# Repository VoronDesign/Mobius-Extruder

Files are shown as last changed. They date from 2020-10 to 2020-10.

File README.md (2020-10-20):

# VORON M4 Extruder

Image of M4

This is the VORON M4 Extruder. It's a dual geared hobbed filament extruder designed for the Voron family of printers. It features a 4:1 belt driven design to provide torque while being able to be near silent. It borrows the best parts of the various extruders we've released over the past 5 years.

Voron Logo

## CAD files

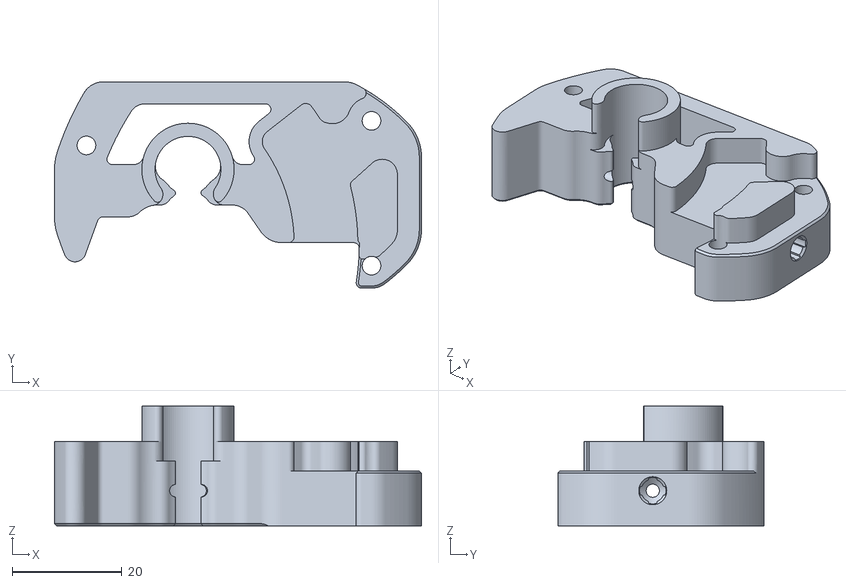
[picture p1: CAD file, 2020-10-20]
STLs/main_body_mirror.stl
66.8 x 37.6 x 21.8

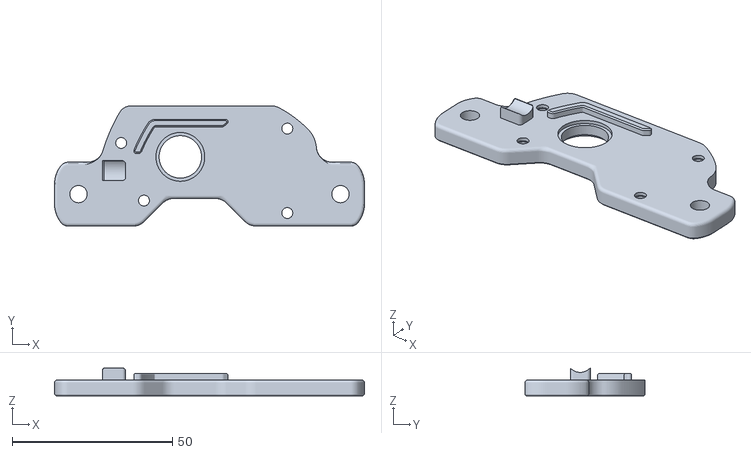
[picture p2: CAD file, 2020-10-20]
STLs/end_plate_mirror.stl
96.8 x 37.6 x 8.60

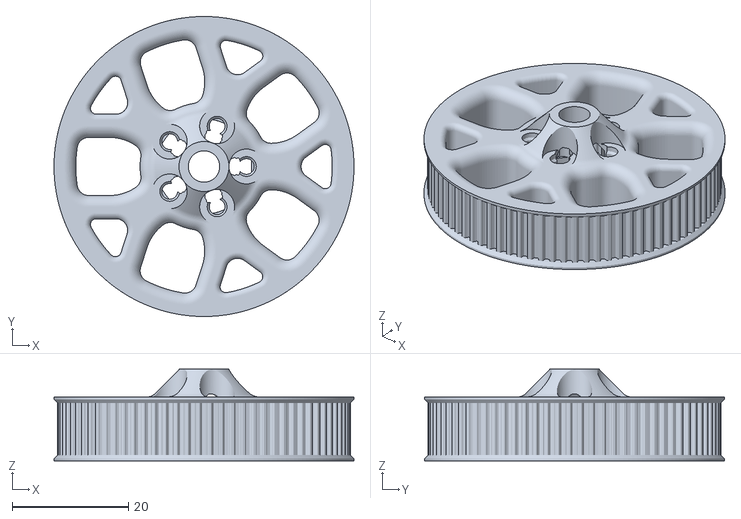
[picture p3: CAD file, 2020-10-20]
STLs/[a]_80t_gear.stl
51.6 x 51.6 x 15.8

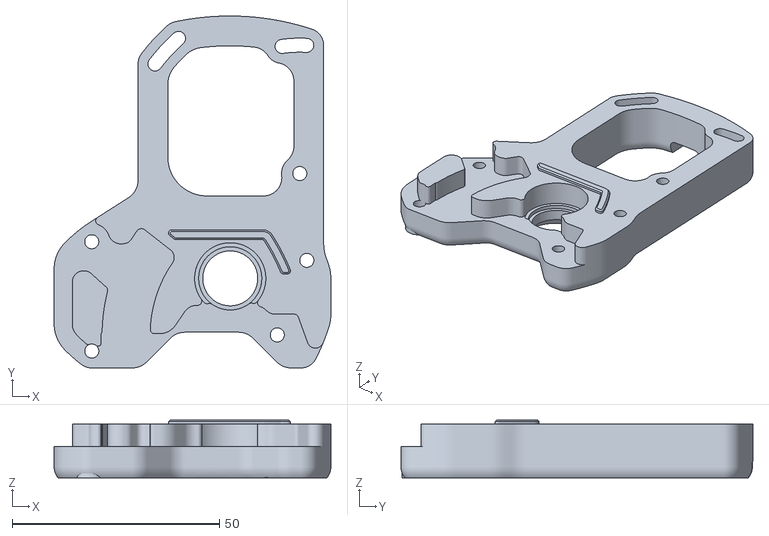
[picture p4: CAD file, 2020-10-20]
STLs/motor_plate_mirror.stl
66.8 x 85.0 x 14.0

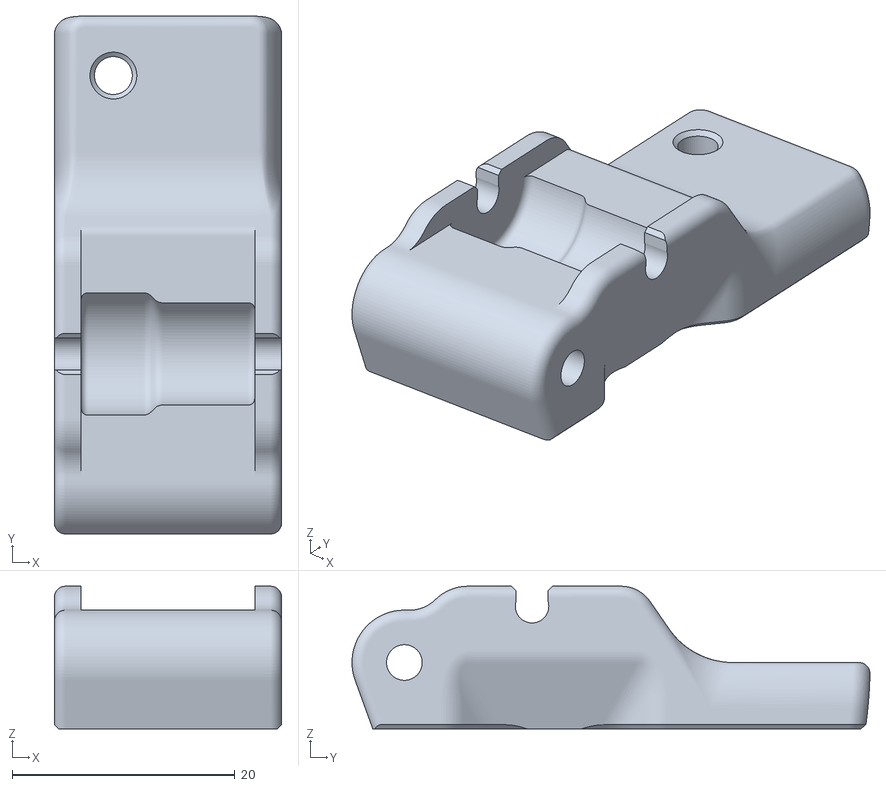
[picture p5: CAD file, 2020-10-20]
STLs/[a]_guidler.stl
20.4 x 46.5 x 12.8

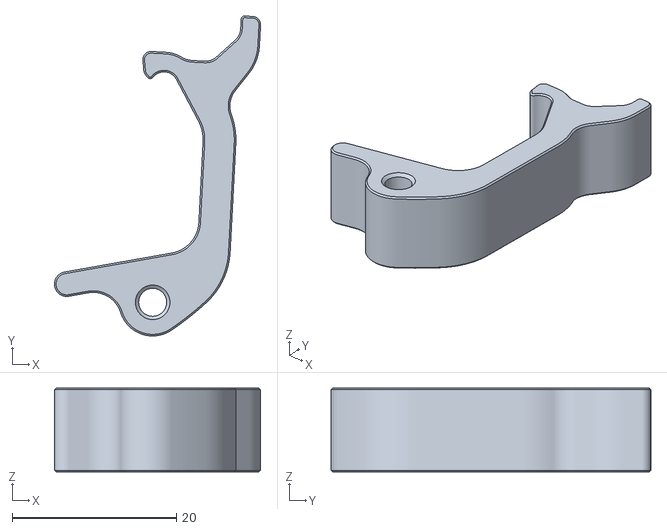
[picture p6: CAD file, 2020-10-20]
STLs/[a]_latch.stl
25.1 x 38.9 x 10.2

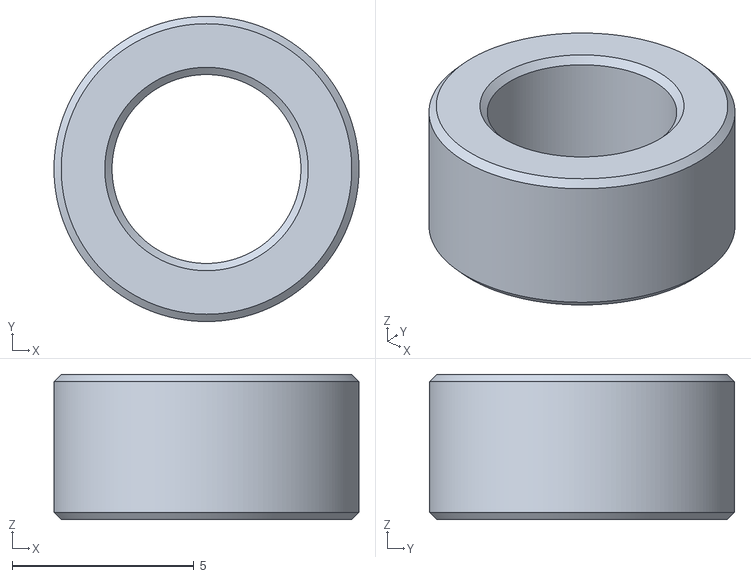
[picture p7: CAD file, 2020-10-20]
STLs/[a]_5x4mm_spacer.stl
8.40 x 8.40 x 4.00

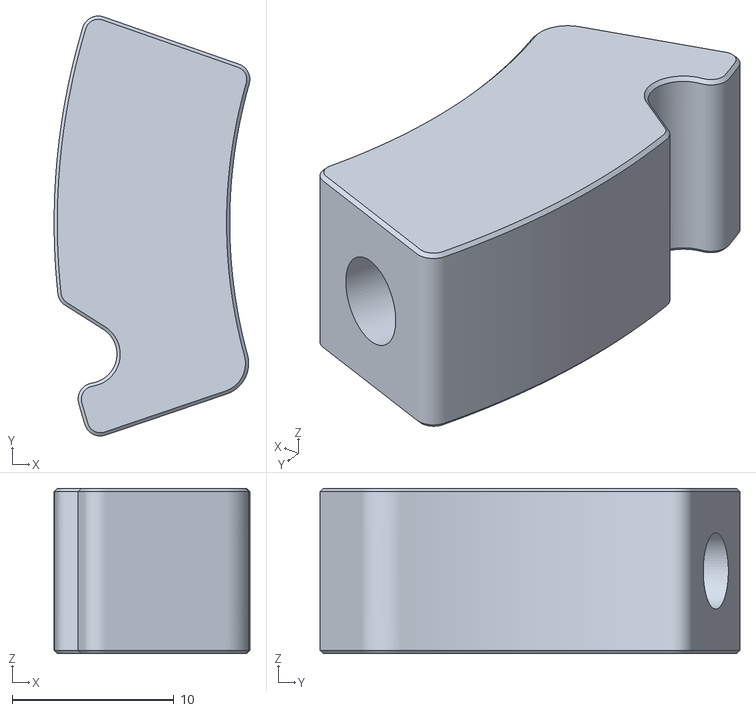
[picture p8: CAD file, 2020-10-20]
STLs/latch_shuttle.stl
12.1 x 25.9 x 10.2

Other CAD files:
STLs/main_body.stl
STLs/end_plate.stl
STLs/[a]_guidler_mirror.stl
STLs/motor_plate.stl
CAD/voron_m4_assembly.f3d

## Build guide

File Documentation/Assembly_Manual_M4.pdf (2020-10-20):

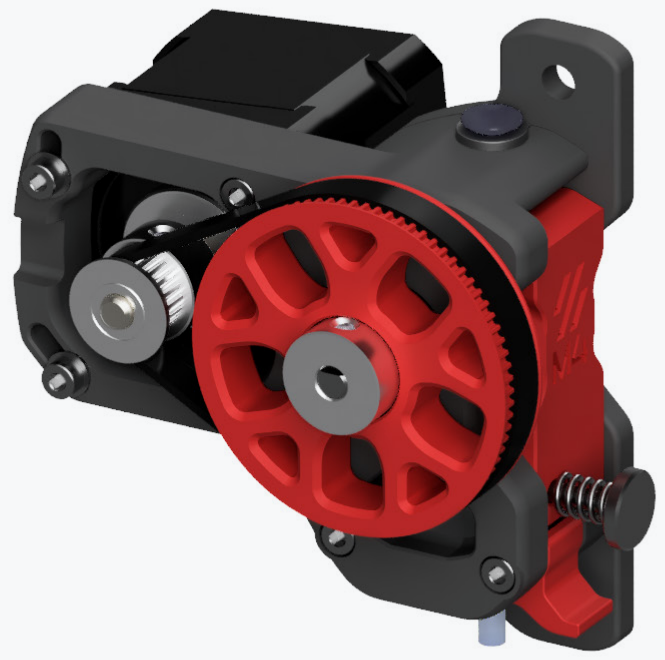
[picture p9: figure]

1

### WWW.VORONDESIGN.COM

VERSION 2020-10-19

# M4 ASSEMBLY MANUAL

## We build space shuttles with gardening tools

so anyone can have a space shuttle of their own.

# VORON

2

INTRODUCTION | WWW.VORONDESIGN.COM

Before you begin on your journey, a word of caution.

In the comfort of your own home you are about to assemble a robot. This
machine can maim, burn, and electrocute you if you are not careful. Please
do not become the first VORON fatality. There is no special Reddit flair for that.

Please, read the entire manual before you start assembly. As you begin wrenching, please check our Discord channels for any tips and questions that may halt your progress.

Most of all, good luck!
THE VORON TEAM

3

INTRODUCTION | WWW.VORONDESIGN.COM

PART PRINTING GUIDELINES
The Voron Team has provided the following print guidelines for you to follow in order to have the best chance at success with your parts. There are often questions about substituting materials or changing printing standards, but we recommend you follow these.

3D PRINTING PROCESS
Fused Deposition Modeling (FDM)

MATERIAL
ABS

LAYER HEIGHT
Recommended: 0.2mm

EXTRUSION WIDTH
Recommended: Forced 0.4mm

INFILL TYPE
Grid, Gyroid, Honeycomb, Triangle or Cubic

INFILL PERCENTAGE
Recommended: 40%

WALL COUNT
Recommended: 4

SOLID TOP/BOTTOM LAYERS
Recommended: 5

PRINT IT FORWARD (PIF)
Often times our community members have issues printing ABS will bootstrap themselves into a VORON using our Print It Forward program. This is a service where approved members with VORON printers can make you a functional set of parts to get your own machine up and running.
Check Discord if you have any interest in having someone help you out.

4

INTRODUCTION | WWW.VORONDESIGN.COM

HOW TO GET HELP
If you need assistance with your build, we’re here to help. Head on over to our Discord group and post your questions. This is our primary medium to help VORON Users and we have a great community that can help you out if you get stuck.

https://discord.gg/voron

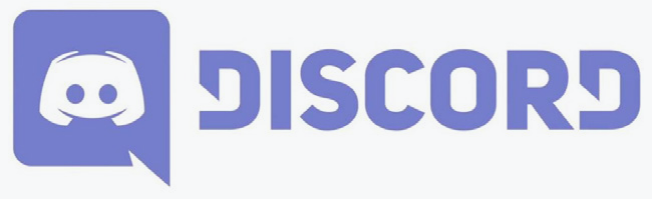
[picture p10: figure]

THIS IS JUST A REFERENCE
This manual is designed to be a simple reference manual. Building a Voron can be a complex endeavour and for that reason we recommend downloading the CAD files off our Github repository if there are sections you need clarification on. It can be sometimes be easier to follow along when you have the whole assembly in front of you.

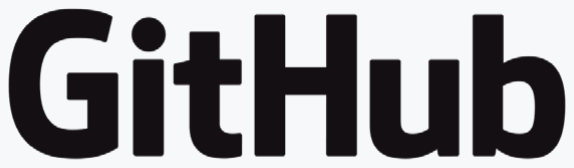
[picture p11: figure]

https://github.com/vorondesign

5

### WWW.VORONDESIGN.COM

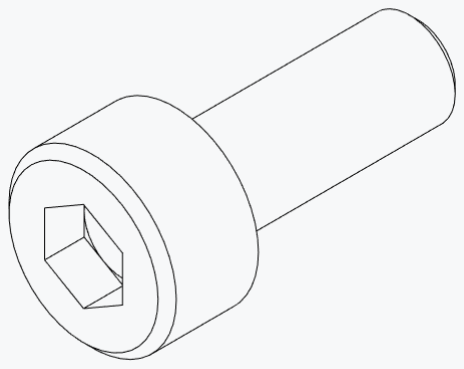
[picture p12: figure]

SOCKET HEAD CAP SCREW (SHCS) Metric fastener with a cylindrical head and hex drive. The most common fastener used on the Voron.

ISO 4762

WASHER
Small metal disc to increase the surface area.

DIN 988

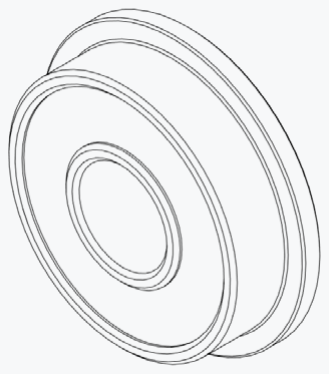
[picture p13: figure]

PULLEY
GT2 pulley used on the motion system of the Voron.

HARDWARE
HEAT SET INSERT
Heat inserts with a soldering tip so that they melt the plastic when installed. As the plastic cools, it solidifies around the knurls and ridges on the insert for excellent resistance to both torque and pull-out.

F695 BEARING
A ball bearing with a flange used in various gantry locations.

GRUB SCREW
Small headless screw with an internal drive.

ISO 4026

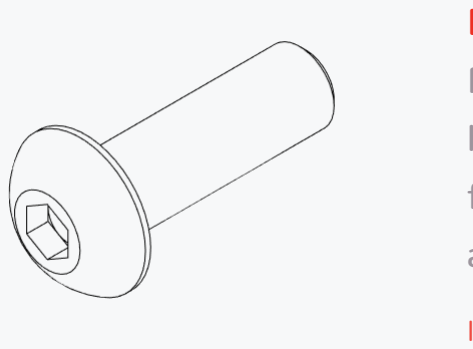
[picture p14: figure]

BUTTON HEAD CAP SCREW (BHCS) Metric fastener with a domed shape head and hex drive. Most commonly found in locations where M5 fasteners are used.

ISO 7380-1

### WWW.VORONDESIGN.COM

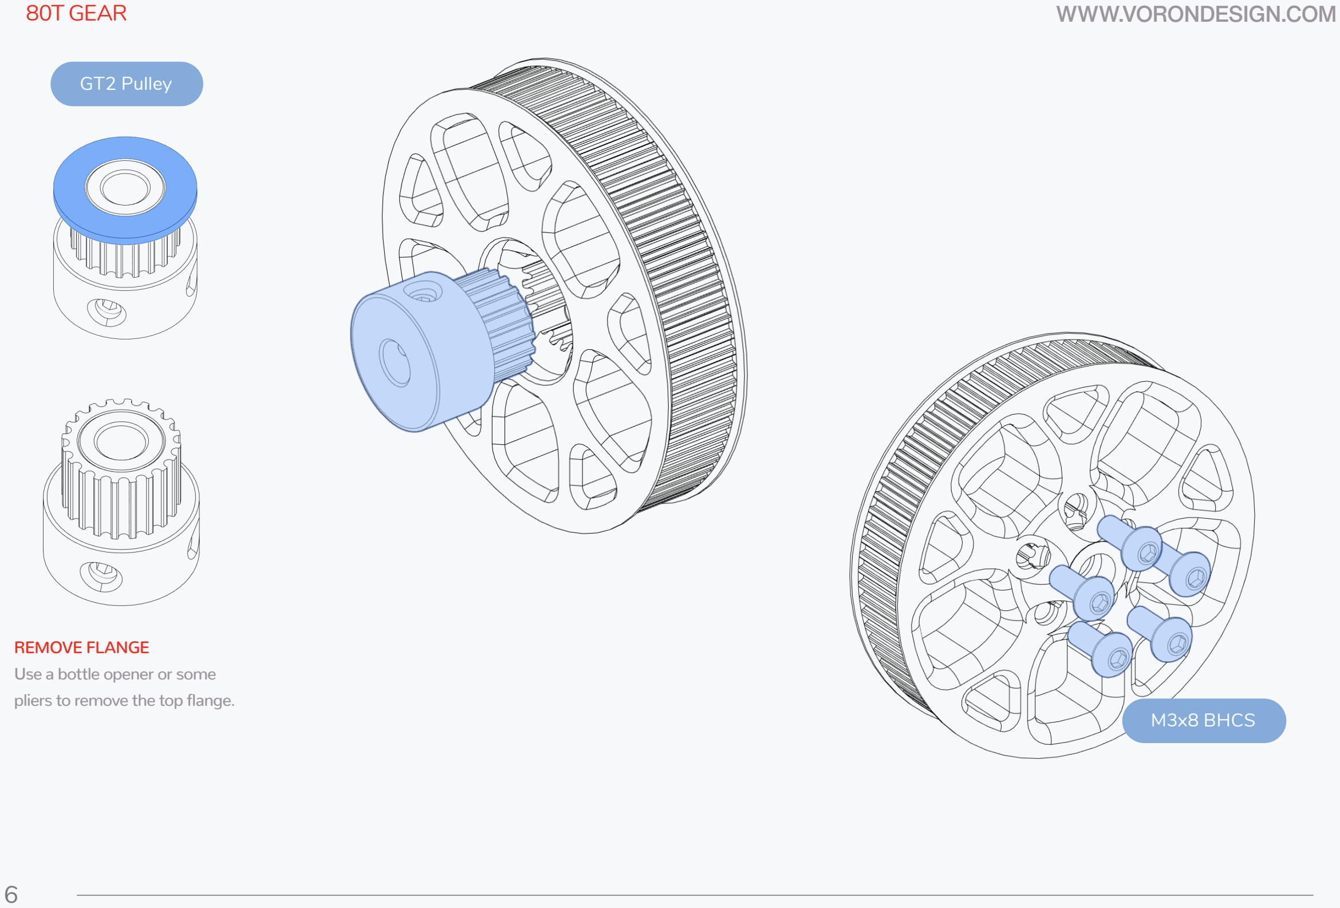
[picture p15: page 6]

6

REMOVE FLANGE
Use a bottle opener or some pliers to remove the top flange.

GT2 Pulley

M3x8 BHCS

80T GEAR

7

### WWW.VORONDESIGN.COM

CHECK BEARING FIT
The bearings must slip on and off the shaft easily. Pressing the bearings on the shaft will damage them. Lightly sand the shaft if required.

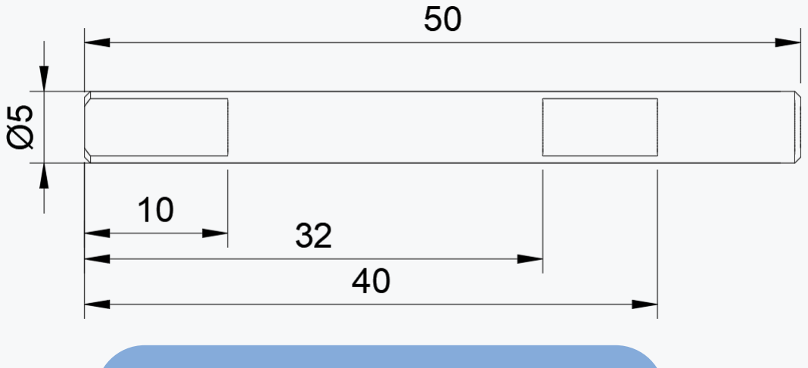
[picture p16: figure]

5x50mm Shaft w/ Flats
F695 Bearing

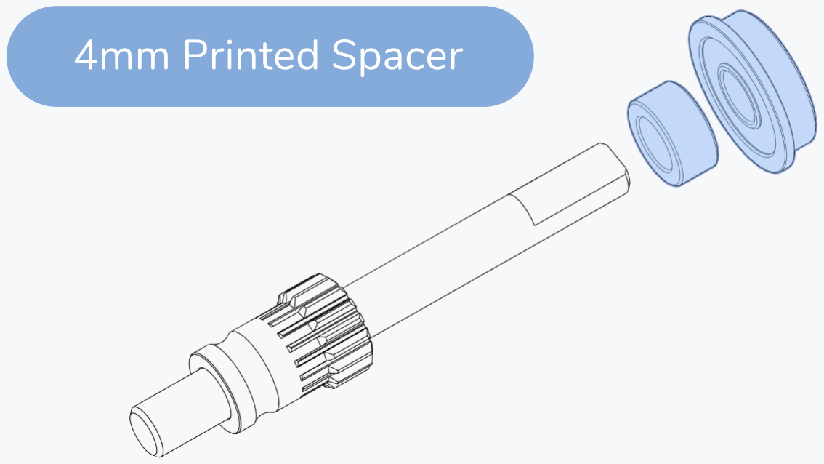
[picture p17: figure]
4mm Printed Spacer

DRIVE GEAR POSITION
Position the drive gear 8mm from the end of the shaft and tighten the grub screw.
Use thread locker.

DRIVE SHAFT

FLAT FACE ON THE SHAFT
Align the flat face of the shaft with the grub screw of the drive gear. If your shaft is fully round make a small flat spot with a file to ensure proper seating.

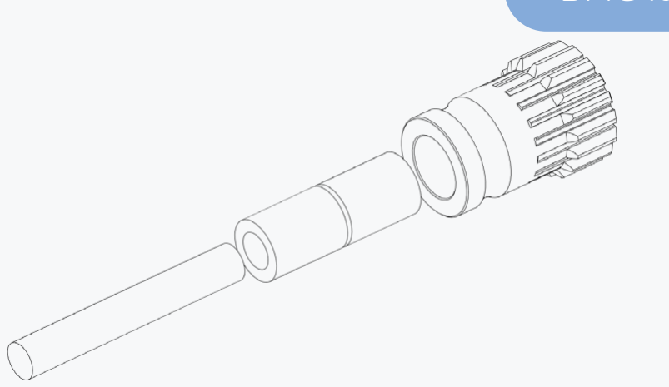
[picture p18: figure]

8

### WWW.VORONDESIGN.COM

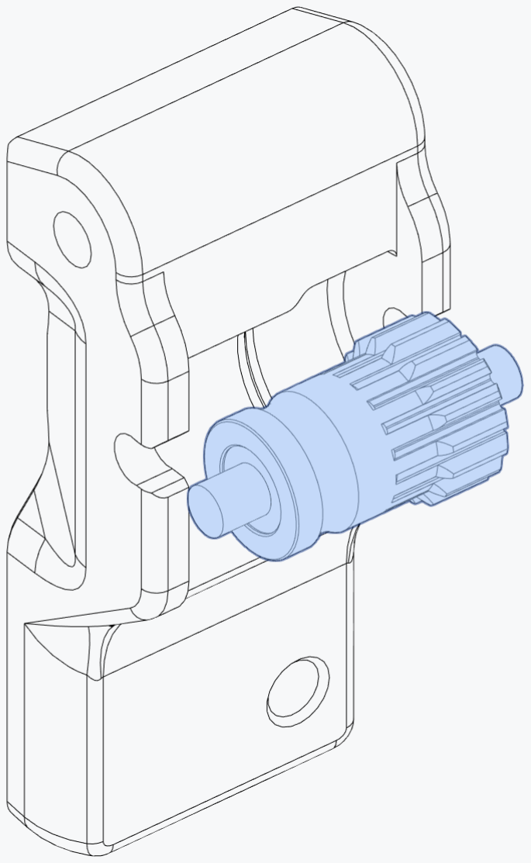
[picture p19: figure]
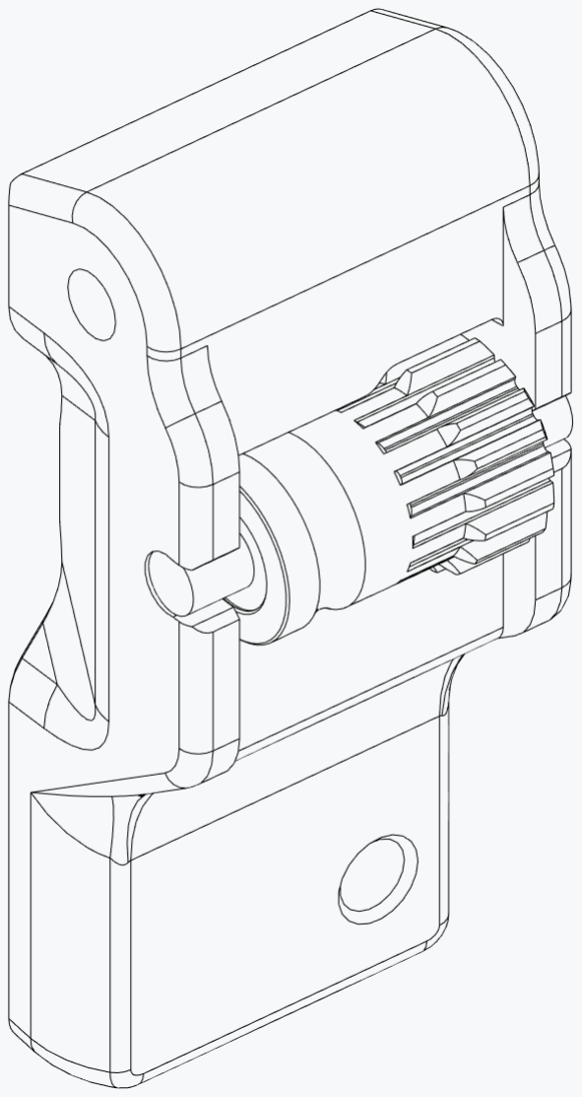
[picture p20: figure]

LUBRICATE BEARINGS
A light lubrication film will help with smooth operation and longevity.

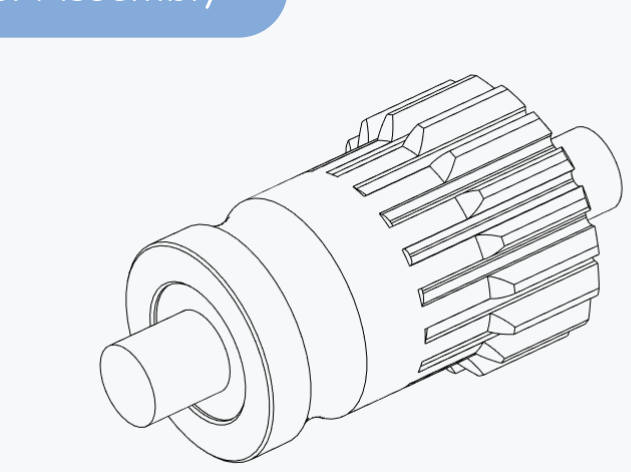
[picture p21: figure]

BMG Idler Assembly

IDLER ASSEMBLY

### WWW.VORONDESIGN.COM

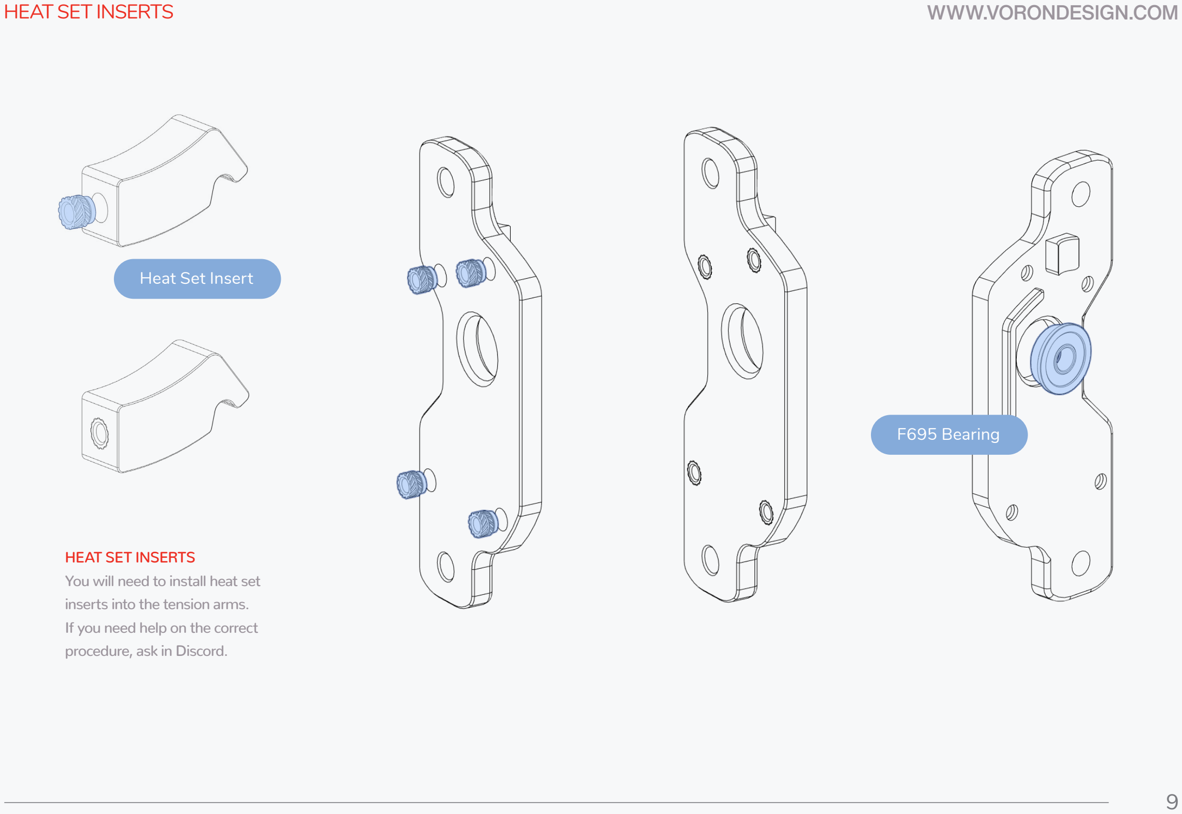
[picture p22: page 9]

9

HEAT SET INSERTS
You will need to install heat set inserts into the tension arms. If you need help on the correct procedure, ask in Discord.

Heat Set Insert

F695 Bearing

HEAT SET INSERTS

BODY ASSEMBLY | WWW.VORONDESIGN.COM

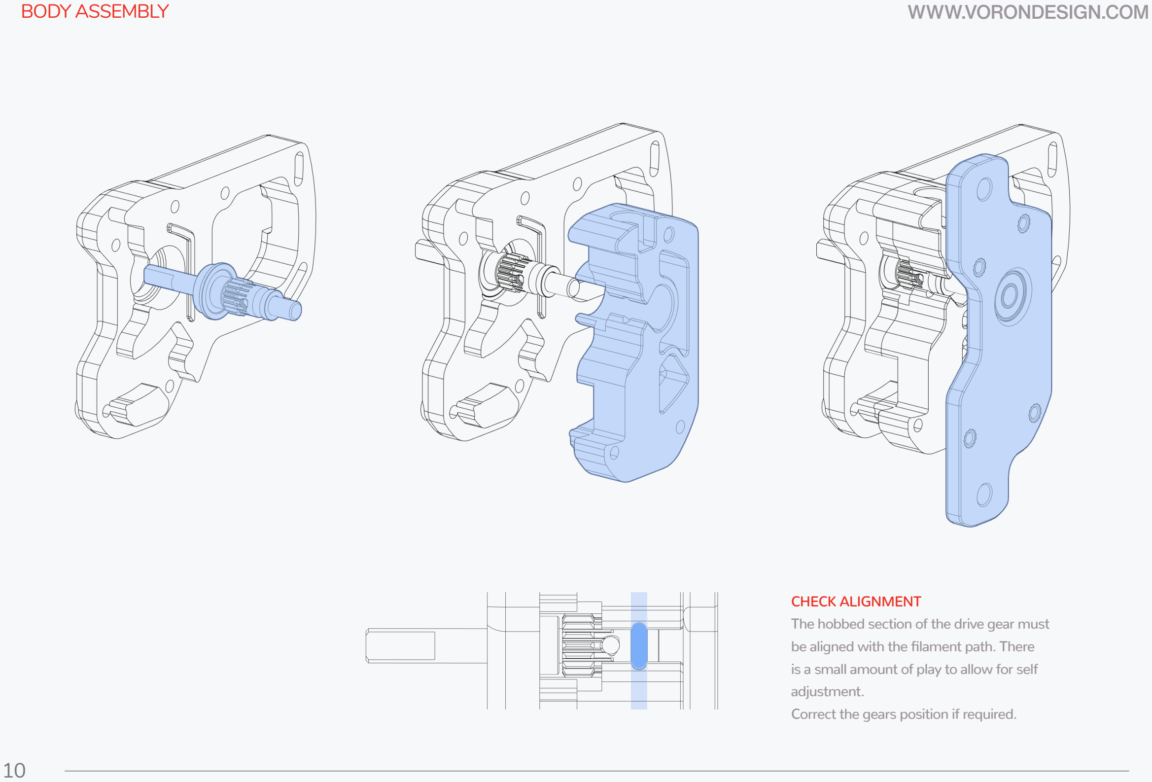
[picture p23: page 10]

10

CHECK ALIGNMENT
The hobbed section of the drive gear must be aligned with the filament path. There is a small amount of play to allow for self adjustment.
Correct the gears position if required.

BODY ASSEMBLY | WWW.VORONDESIGN.COM

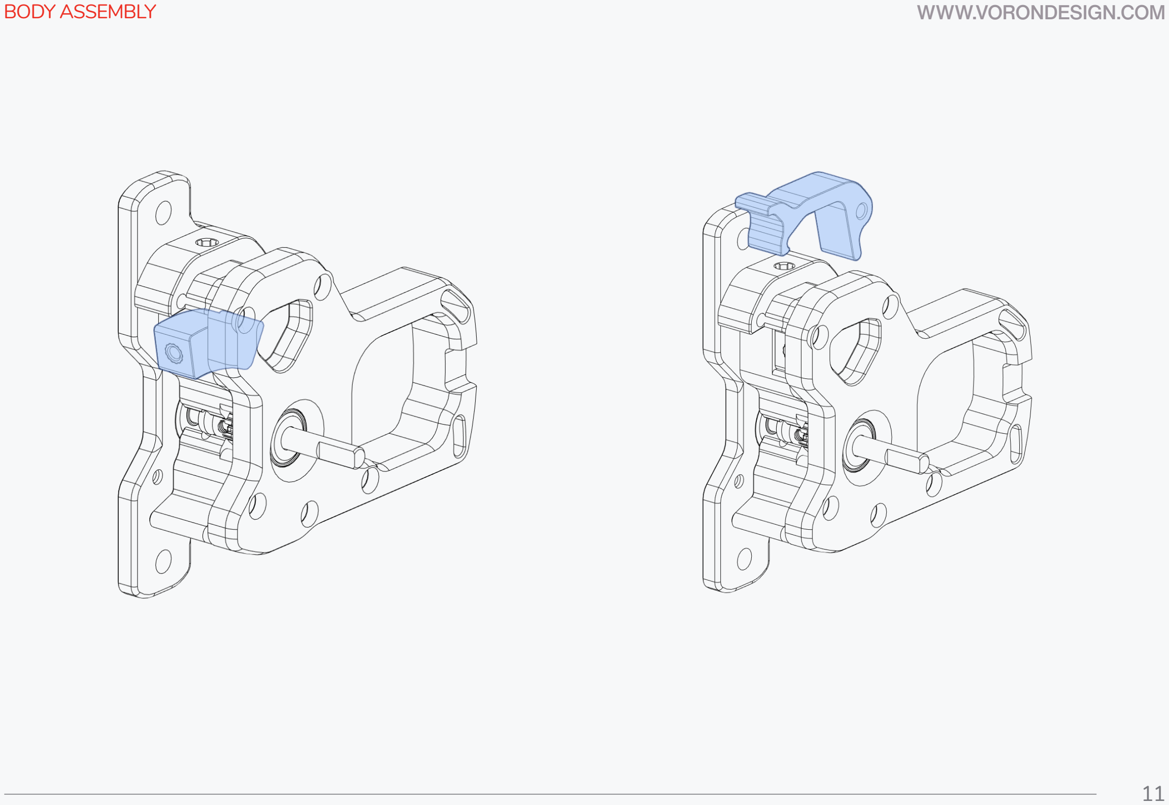
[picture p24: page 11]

11

12

### WWW.VORONDESIGN.COM

BODY ASSEMBLY

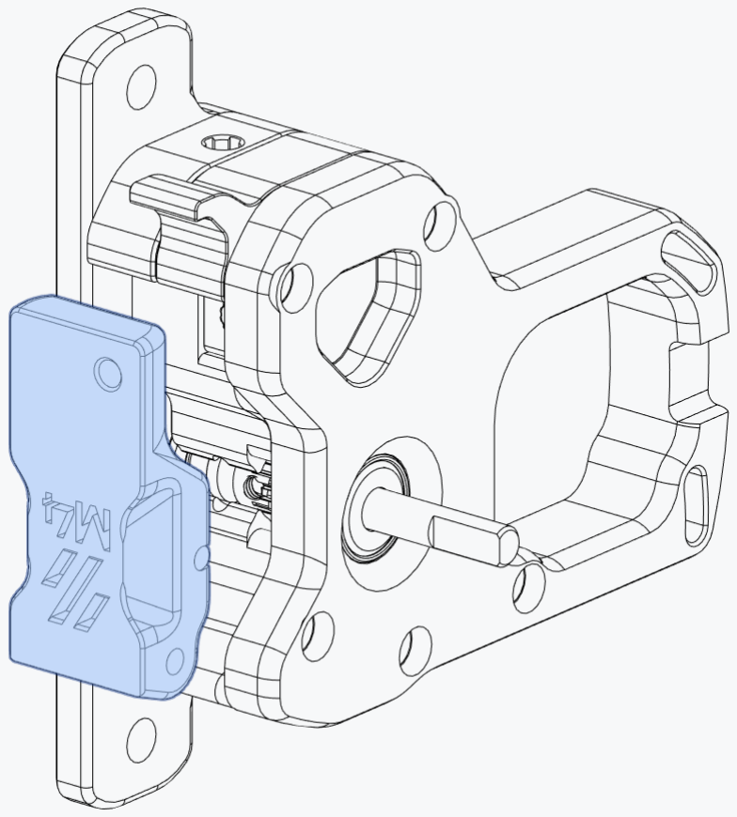
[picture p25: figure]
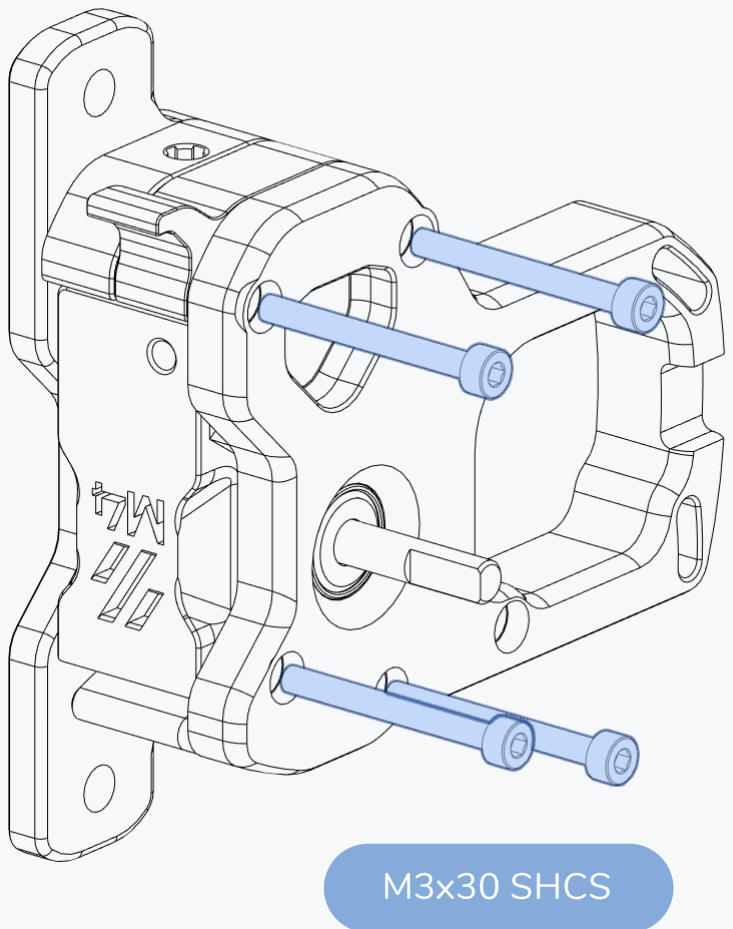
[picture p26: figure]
M3x30 SHCS

### WWW.VORONDESIGN.COM

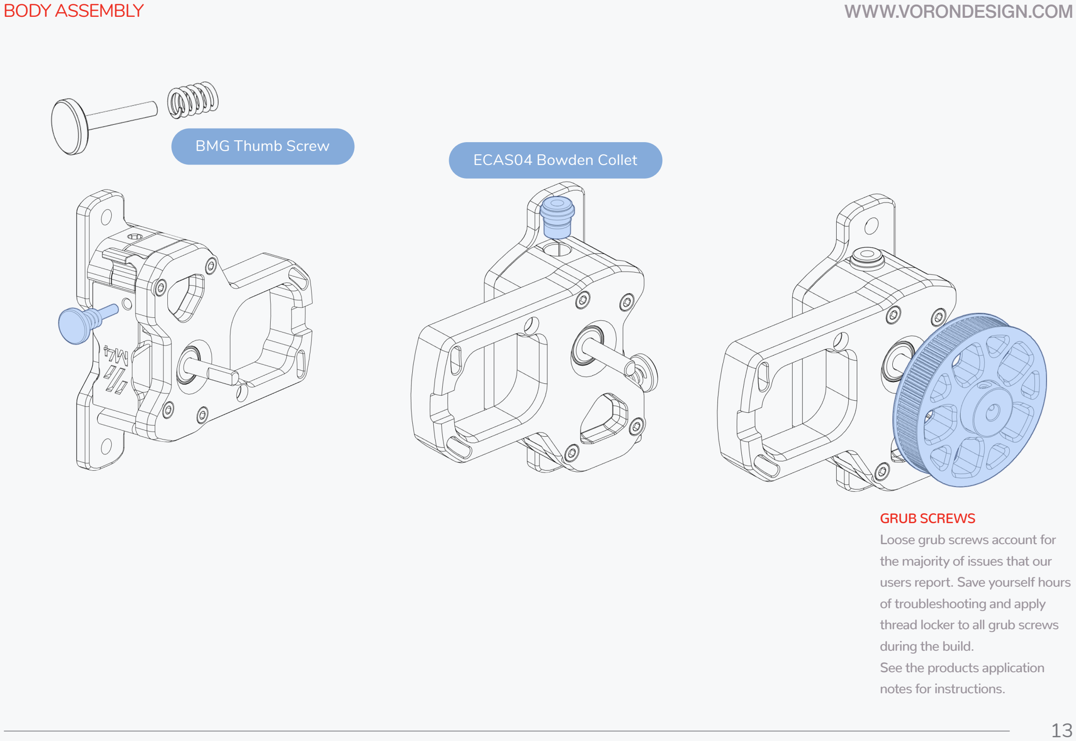
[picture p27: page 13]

13

GRUB SCREWS
Loose grub screws account for the majority of issues that our users report. Save yourself hours of troubleshooting and apply thread locker to all grub screws during the build.
See the products application notes for instructions.

BMG Thumb Screw
ECAS04 Bowden Collet

BODY ASSEMBLY

### WWW.VORONDESIGN.COM

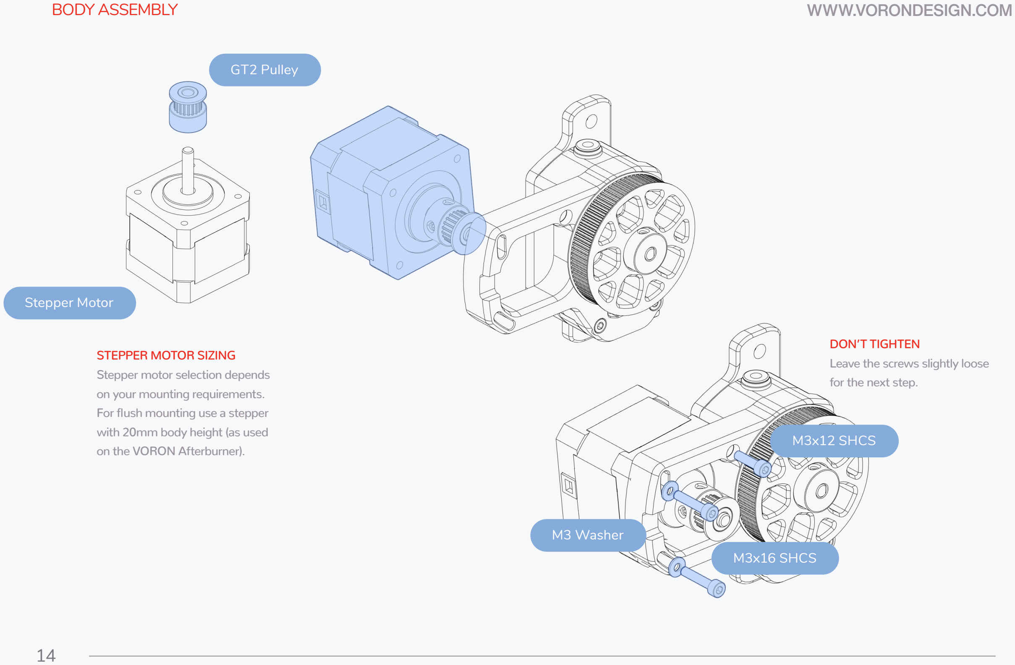
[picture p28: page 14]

14

GT2 Pulley

Stepper Motor

STEPPER MOTOR SIZING
Stepper motor selection depends on your mounting requirements. For flush mounting use a stepper with 20mm body height (as used on the VORON Afterburner).

M3x12 SHCS

M3x16 SHCS

M3 Washer

DON’T TIGHTEN
Leave the screws slightly loose for the next step.

BODY ASSEMBLY

15

### WWW.VORONDESIGN.COM

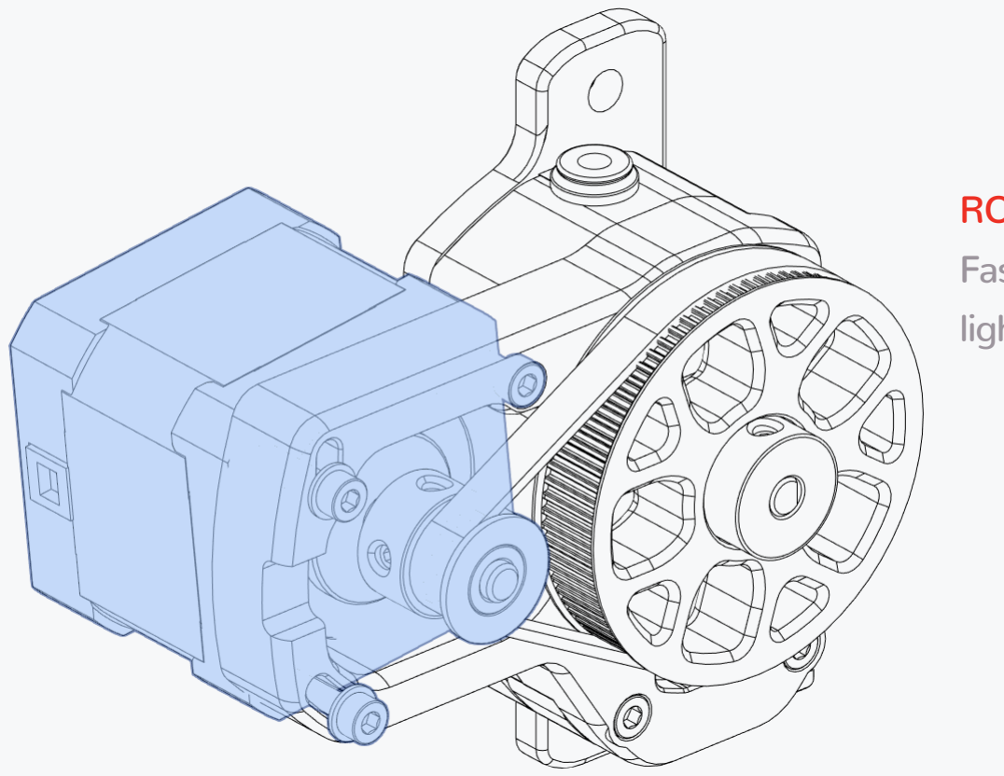
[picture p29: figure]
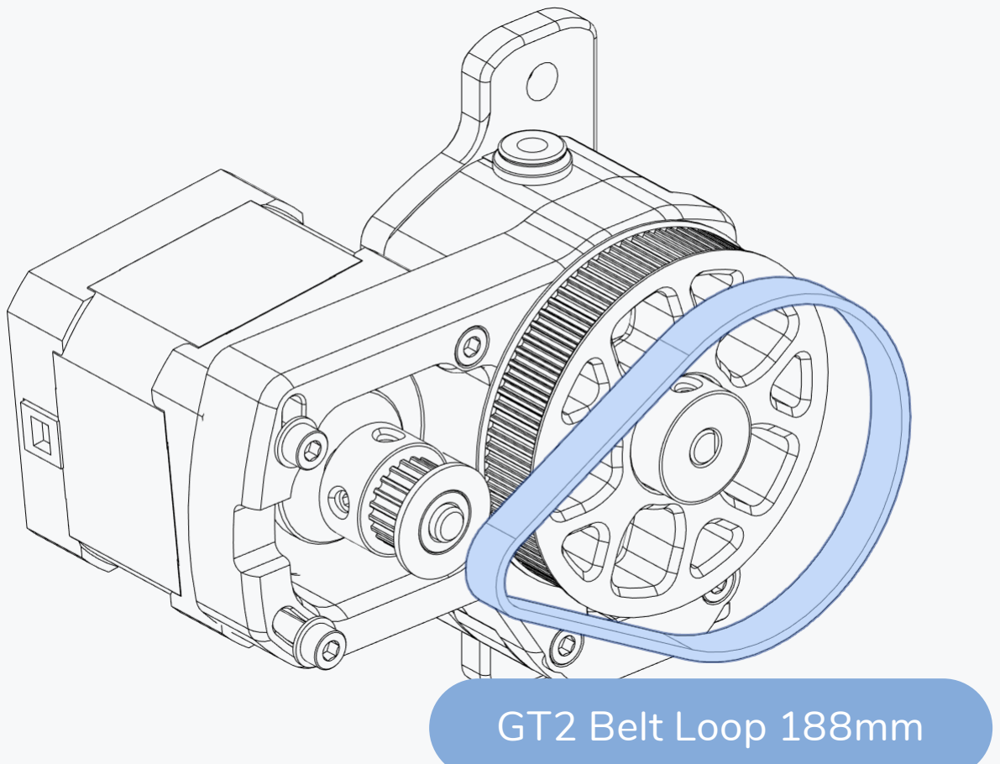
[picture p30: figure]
GT2 Belt Loop 188mm

ROTATE STEPPER TO TIGHTEN
Fasten the screws after applying a light pressure to tighten the belt.

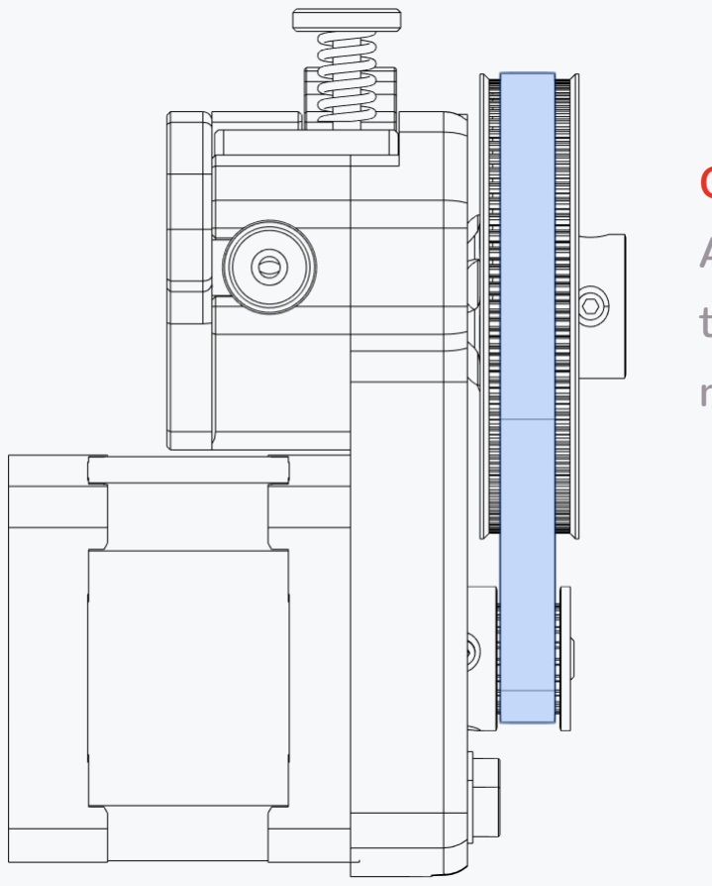
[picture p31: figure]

CHECK ALIGNMENT
Adjust the position of the pulley on the stepper if required. Belt must not rub on the flanges.

DRIVE BELT & ALIGNMENT

16

### WWW.VORONDESIGN.COM

Github
https://github.com/vorondesign

Website
www.vorondesign.com

Discord
https://discord.gg/voron

# VORON

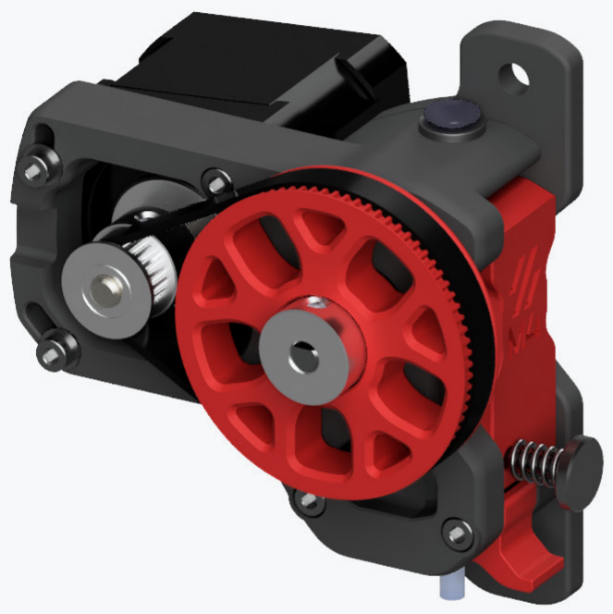
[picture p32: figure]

17

### WWW.VORONDESIGN.COM

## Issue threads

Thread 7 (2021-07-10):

80-Tooth to 20-Tooth gear connection screw: Size mismatch between sources

SobhanAbedi, 2021-07-10:
Hi. The main issue is with VoronDesing website. I think since the website is linked under VoronDesign GitHub account, it's ok to post this issue here.
The screw needed for connecting the 80-Tooth gear to 20-Tooth gear is said to be M3x6 in the BOM and Sourcing guide but in the manual and .STEP file it is M3x8. Since M3x8 doesn't have any clearance issues in the CAD, I guess they should both work fine but it would be better if the mismatch is fixed.

telxoid, 2021-08-20:
Confirmed and pointed out by another user.  Either should work fine, but best to eliminate confusion.

Closed 2022-07-19.

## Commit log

2018-09-08 Mobius 2 Extruder
    [80t_press_bolt_head_side.STL, 80t_press_hex_side.STL, _belt_clip_x2.stl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]
2018-10-17 replacing 80T STL's
    [80t_ring_gear.stl, _vlock_a.stl, _vlock_b.stl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]
2018-10-17 sorry about earlier. I didn't mean to touch you in that way. :(
    [_vlock_a.stl, _vlock_b.stl, _vlock_ring_80t.stl]
2019-01-27 Branch reorg for Mobius
    [01_home_z_mech.g, 01_physics_z_100.g, 01_physics_z_1000.g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]
2019-02-20 Removing a space cause it bothers me
    [_external_gear_spacer.stl, _front_idler_arm.stl, _internal_gear_spacer.stl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]
2019-02-20 VORON Mobius3 Release
    [_4mm_spacer_x2.stl, _front_idler_arm.stl, _latch.stl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]
2019-02-20 Cleaning up
    [_4mm_spacer_x2.stl, _external_gear_spacer.stl, _front_idler_arm.stl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]
2019-07-08 update license, remove M3 branch, condense to 1 branch
    update license, remove M3 branch, condense to 1 branch
    [_4mm_spacer_x2.stl, _front_idler_arm.stl, _latch.stl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]
2019-07-08 Delete base_mini.stl
    remove ancilary part
    [base_mini.stl]
2019-08-27 accent_ to [accent]_
    accent_ to [accent]_
    [[accent]_4mm_spacer_x2.stl, [accent]_external_gear_spacer.stl, [accent]_front_idler_arm.stl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]
2019-08-27 [accent]_ to [a]_
    [accent]_ to [a]_
    [[a]_4mm_spacer_x2.stl, [a]_external_gear_spacer.stl, [a]_front_idler_arm.stl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]
2019-09-21 Release M3dot1 to the World
    Release M3dot1 to the World
    [[a]_4mm_spacer_x2.stl, [a]_4mm_spacer_x2_Rev1.stl, [a]_80t_hubbed_gear_ultralight_Rev1.STL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]
2019-10-24 Publishing CAD files for Mobius 3.1
2020-10-20 Release package for VORON M4 Extruder
    [BMGobius Body A.SLDPRT, BMGobius Body A.STEP, BMGobius Body A.STL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]
2020-10-20 Adding VORON M4 CAD
    [voron_m4_assembly.f3d]
